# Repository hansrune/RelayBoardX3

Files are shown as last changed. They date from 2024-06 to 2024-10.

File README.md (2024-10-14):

# Relay board X3

Work in progress / still a prototype...

A DYI 3x relay board based on ESP32c3. This is a multi purpose board used for:

- `Garage doors` - controlling dual garage doors and control use of external switches
- `Ventilator / 1-phase small motor` 1-2-3 speed control. 

This board is tested with ESPhome and ESPEasy [firmware](#firmwares) (build instructions below), and is easily used with home automation systems that support MQTT auto discovery, the native Home Assistant API, and the many [controllers that ESPEasy supports](https://espeasy.readthedocs.io/en/latest/Controller/_Controller.html)

## Introduction

Some of the main features and benefits

- **3x galvanic isolated relays**
- **Car precense sensors**
    - Ultrasound sensor option
- **I2C support**
    - An I2C pin header with power supply is available to use with I2C sensors
    - ... or you can use the same GPIO pins for any other purpose of your choise
- **WiFi based**
    - This is almost a must have for most home automation systems
    - OTA support
    - Configuration backup, restore and bulk updates.
- **Firmware of your choise**
    - ESPEasy with Domoticz over http. Device creation uses virtual sensors
    - ESPEasy with Domotics and Home Assistant via MQTT. Device creation uses a MQTT configuration text file.
    - ESPHome to Home Assistant via MQTT and auto discovery
    - ESPHome to Domoticz via MQTT and auto discovery
    - ... and as the hardware supports using both Arduino and ESP-IF development kits, almost any other firmware can be created.
- **Seed Studio XIAO ESP32C3**
    - This device is shielded and comes with an external IPX antenna connector
    - FCC and CE regulations approved

<!--
## Setup and mounting - perhaps add later
-->

## Indicators

Each of the four valve outputs has a LED indicator at the back of the PCB

- LED D11 will indicate low level input from the flow meter
- LED D1
  - no change indicates out of power, device death/freeze or other
  - a duty cycle 1:1 will indicate a reset is ongoing
<!--
  - will blink with a duty cycle 1-4 or 4-1 to indicate valve closed or open
-->

## Implementation and design

The schematic diagram is [available here](KiCad//RelayBoardX3-schema-2.0.pdf). The [KiCad EDA](https://www.kicad.org/) project is in the [same folder](./KiCad)

### GPIO pin usage

| PIN | Capabilty | Function |
|---|---|---|
| GPIO2 | Acticve low output | LED D8 - not used |
| GPIO3 | Input with pull-up | J7 pin 2 |
| GPIO4 | Input with pull-up | J7 pin 1 |
| GPIO5 | Active high output | Relay 1 |
| GPIO6 | Active high output | Relay 2 |
| GPIO7 | I2C pulled up | SDL |
| GPIO8 | I2C pulled up | SDA |
| GPIO9 | Active low out | LED D8 - status |
| GPIO10 | Active high output | Relay 3 |
| GPIO20 | RX / 1-wire | Serial or 1-wire sensor or ultrasound |
| GPIO21 | TX / 1-wire | Serial or 1-wire sensor or ultrasound |

## Hardware - getting started

This project uses my [KiCad-lib-ESP32 repository](https://github.com/hansrune/KiCad-lib-ESP32.git) as a [git submodule](https://www.git-scm.com/book/en/v2/Git-Tools-Submodules). To check this out, use the following:

```bash
git clone --recurse-submodules https://github.com/hansrune/RelayBoardX4.git 
```

### Materials used

This project uses the [Seed Studio XIAO ESP32C3 RISC-V module](https://www.seeedstudio.com/Seeed-XIAO-ESP32C3-p-5431.html). This tiny device has proven to be more reliable than most ESP8266 modules used in earlier versions. This module also comes with an IPX connector for connecting an external antenna, and is delivered with a simple external antenna for good range. This device is also EMI shielded and certified.

Any available 12V DC power supply delivering 500mA or more should do for the control board. You will need to add the total power draw for the relays

There are many options and possible pinouts for DC-DC converters for the 12V to 5V conversion. A linear regulator (L7805) will need a heatsink, so a DC-DC converter is recommended.

<p align="center">
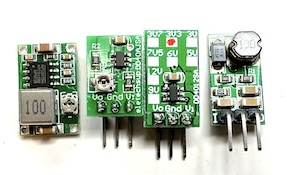
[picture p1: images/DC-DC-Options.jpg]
    
</p>

The MOSFETs need a low Vgs trigger voltage, i.e. well under 3V on full load. I have used Si2302/N025P for the N-channel, SOT-23 package.

Resistors are 0805 size. Screw terminals are 3.5mm, which is a tight fit when ferrules are being used.

For more information, use [this KiCad BOM](KiCad/RelayBoardX3-BOM.csv)

## Hardware assembly

Soldering a prototype by hand is possible if you have a steady hand and a small solder iron tip. A microscope is recommended to inspect the solder joints properly.

Recommend to do the SMD parts first, then other components. 

### Hardware tests

You should test at least the following **before adding the ESP32 module**:

- Attach a battery and check that the valve can be operated both NO and NC
- Add power and check that 5V conversion is OK
- Apply 5V to GPIO 5, 6, and 10 in turn to check that the output works with the relay LED indicators

## Firmwares

### ESPHome

ESPHome firmware can be set up from [this ESPHome configuration repository](https://github.com/hansrune/esphome-config) using the `test_relayx3_garage.yaml` or `test_relayx3_motor.yaml` file as a template

Follow the [README](https://github.com/hansrune/esphome-config) for instructions on what you will likely want to change.

By default, MQTT auto discovery is being used. This should work out of the box with Home Assistant, Domoticz and other that support [Home Assistant MQTT Auto Discovery](https://www.home-assistant.io/integrations/mqtt/#mqtt-discovery)

#### Garage doors control

In Home Assistant, the garage door controls can look like this:

<p align="center">
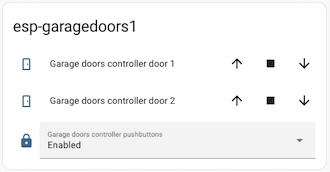
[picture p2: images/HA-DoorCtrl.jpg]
    
</p>

... and the closed state end stop sensors:

<p align="center">
    
</p>

#### Motor control

In Home Assistant, the device has this simple selector:

<p align="center">
    
</p>

### ESPEasy

ESPEasy can be used with a number of different controllers / home automation systms. A custom firmware build description is [available here](https://github.com/hansrune/ESPEasy-custom/blob/builds/custom/mega-20240822-1/README-custombuilds.md)

ESPEasy requires many settings. For configuration settings and rule files, you can upload the below sets of files. Please make sure to change name, unit number, controller IP addresses, NTP, syslog host and latitude/longitude. This configuration uses both a MQTT controller and a Domoticz controller. Change to what you need.

- For the garage control, use the files under [this page](./ESPEasy/garage)
- For the motor/ventilator control, use the files under [this page](./ESPEasy/motor/config.dat

## Wiring

### Dual garage door wiring

This dual garage door setup uses a pulse driven elevator, and has end stop switches for the closed position. There is no end stops for the open position, meaning that the open state simply reflects not closed.

A `RX-Multi` receiver is used in parallel with the relay board. This is operated by remote control units from a car.

We have outdoor push buttons to operate the garage doors. These are disabled via relay #1 when our home alarm state is away or night. The power on state is that these buttons are enabled.

<p align="center">
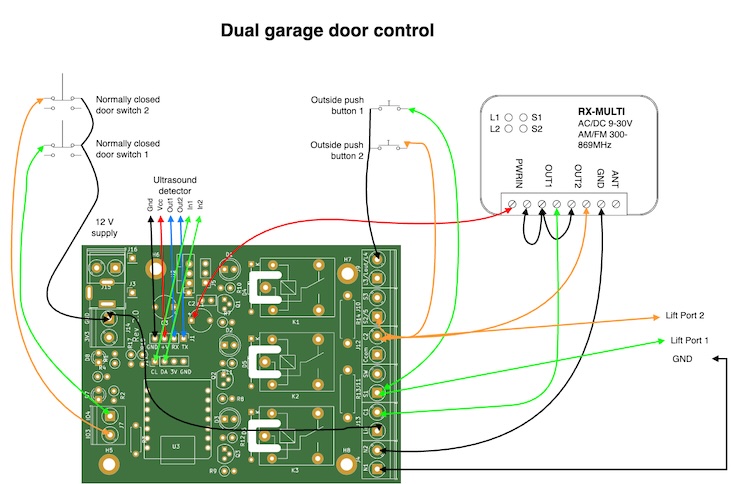
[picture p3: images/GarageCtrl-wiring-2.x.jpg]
    
</p>

### Motor control wiring

This setup is a simple 1-2-3 speed motor control for a ventilator. Can work in parallel with a 1-2-3 switch, where you will get the highest speed selected via contoller or switch.

<p align="center">
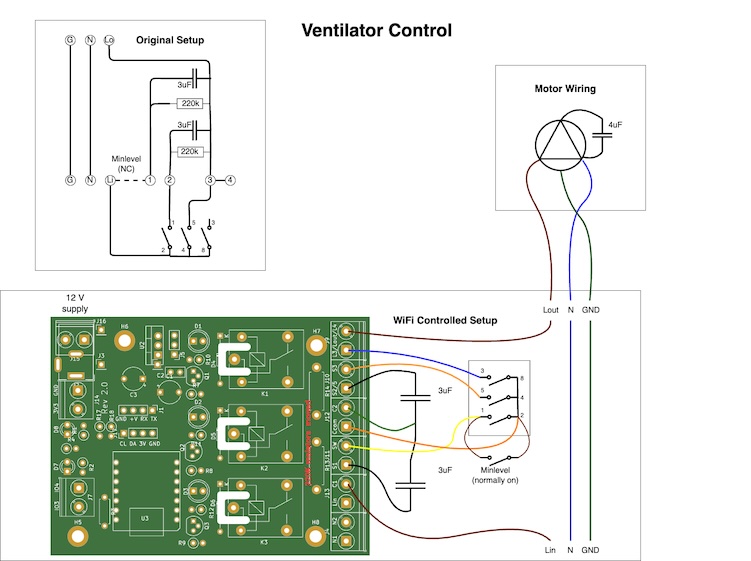
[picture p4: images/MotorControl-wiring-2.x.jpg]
    
</p>

## Licensing

This project is licensed under the [GNU General Public License v3.0](GNU-LICENSE-V3.txt) for the software, [CERN-OHL-W](OHL-LICENSE.txt) for the hardware, and [CC BY-SA](CC-BY-SA-LICENCE.txt) for the documentation and ideas.

<p align="center" width="100%">
    
</p>

<!-- 
| **Open Source Licenses** | |
| ---|---|
| Hardware | [CERN-OHL-W](OHL-LICENSE.txt) |
| Software | [GNU General Public License v3.0](GNU-LICENSE-V3.txt) |
| Documentation / idea | [CC BY-SA](CC-BY-SA-LICENCE.txt) |
-->

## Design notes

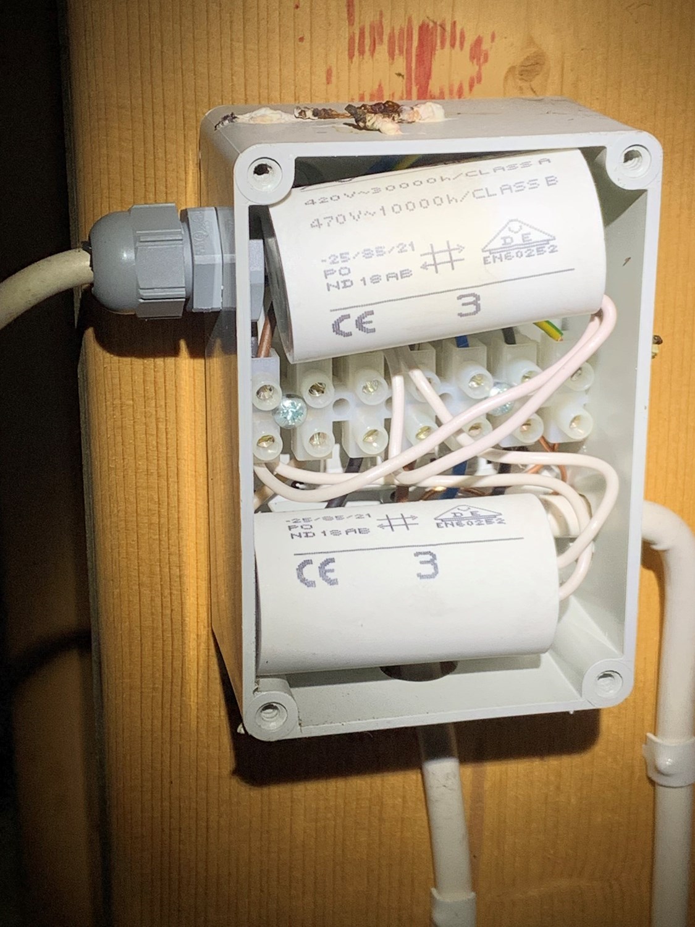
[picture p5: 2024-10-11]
KiCad/vendorinfo/ULVbox.jpg

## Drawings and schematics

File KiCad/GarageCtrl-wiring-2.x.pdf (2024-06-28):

# Dual garage door control

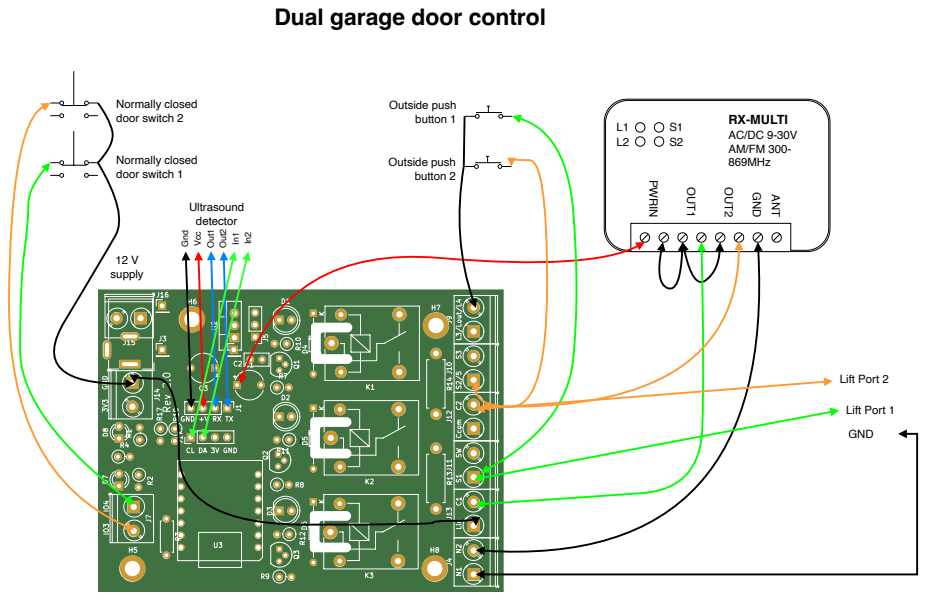
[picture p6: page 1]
RX-MULTI; AC/DC 9-30V AM/FM 300- 869MHz; PWRIN; OUT1; OUT2; GND; ANT; Lift Port 2; Lift Port 1; Outside push button 1; Outside push button 2; Normally closed door switch 2; Normally closed door switch 1; 12 V supply; Ultrasound detector; Gnd; Vcc; Out1; Out2

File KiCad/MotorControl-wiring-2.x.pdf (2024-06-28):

# Ventilator Control

### Original Setup

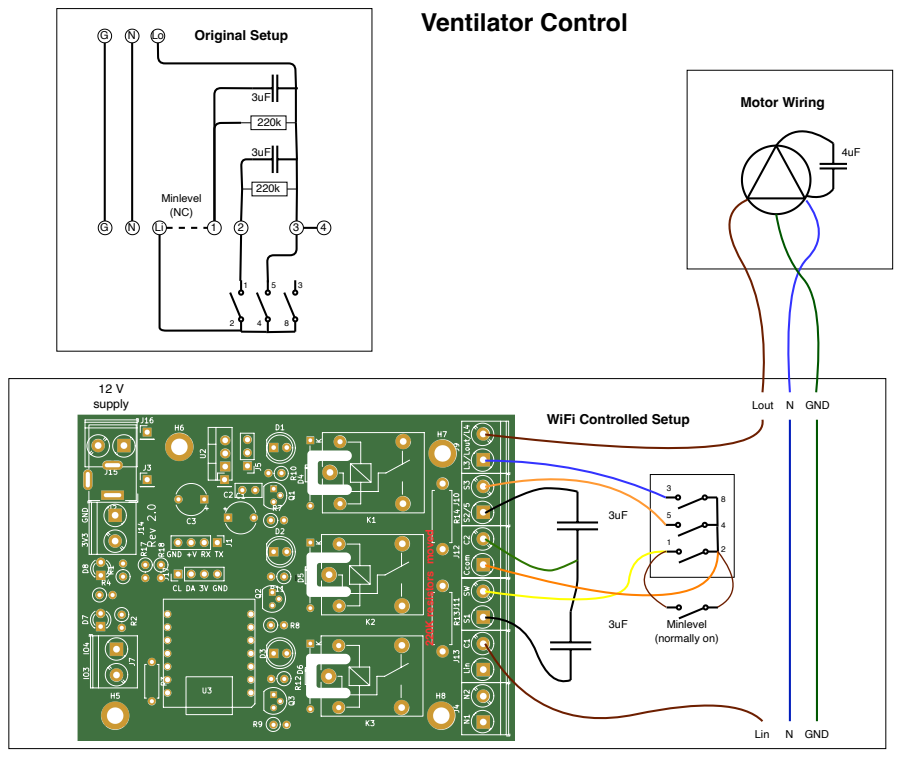
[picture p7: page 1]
12 V supply; Lin; N GND; Lout N GND; Minlevel (normally on); 220K resistors moved; Minlevel (NC); Motor Wiring

WiFi Controlled Setup

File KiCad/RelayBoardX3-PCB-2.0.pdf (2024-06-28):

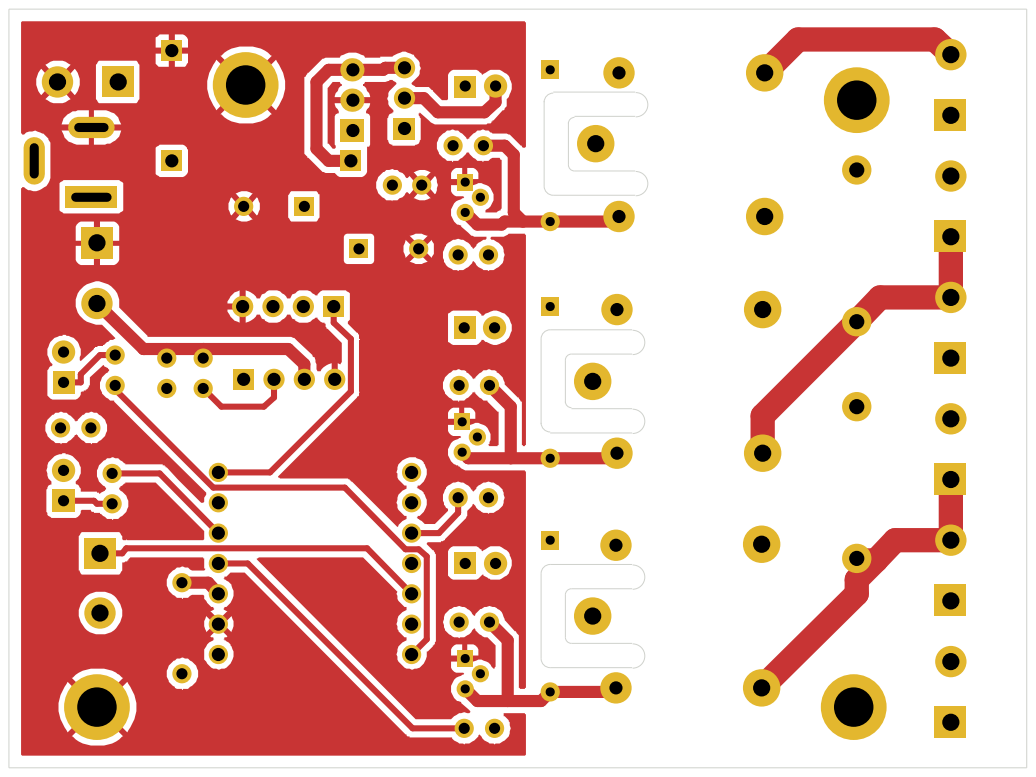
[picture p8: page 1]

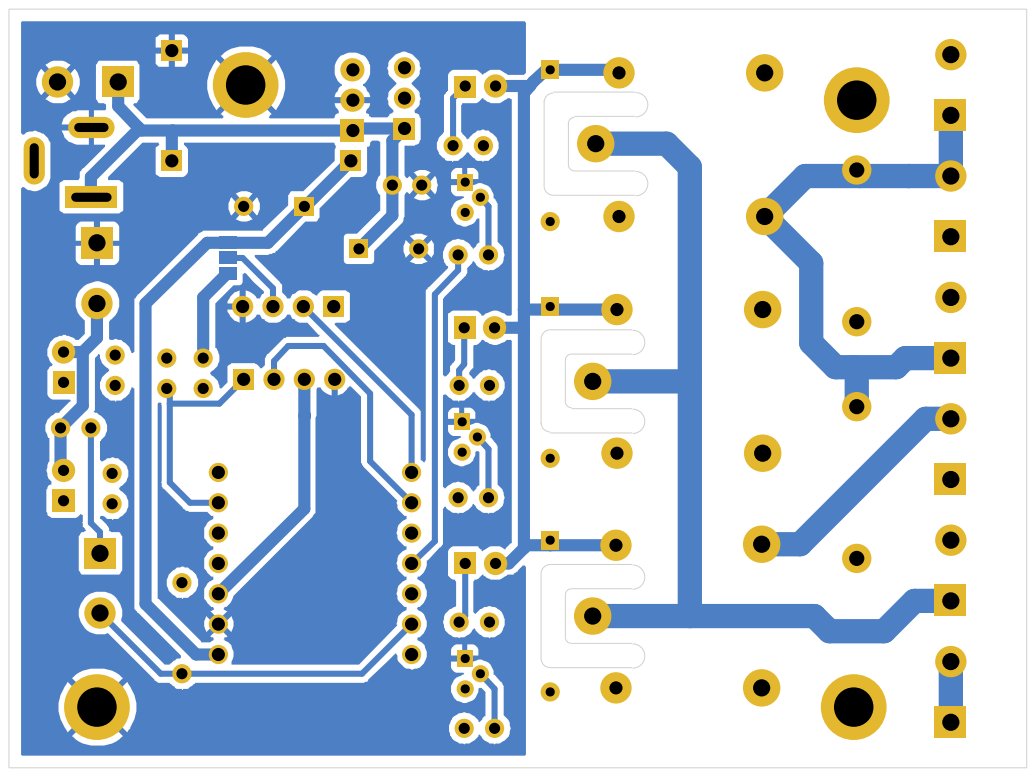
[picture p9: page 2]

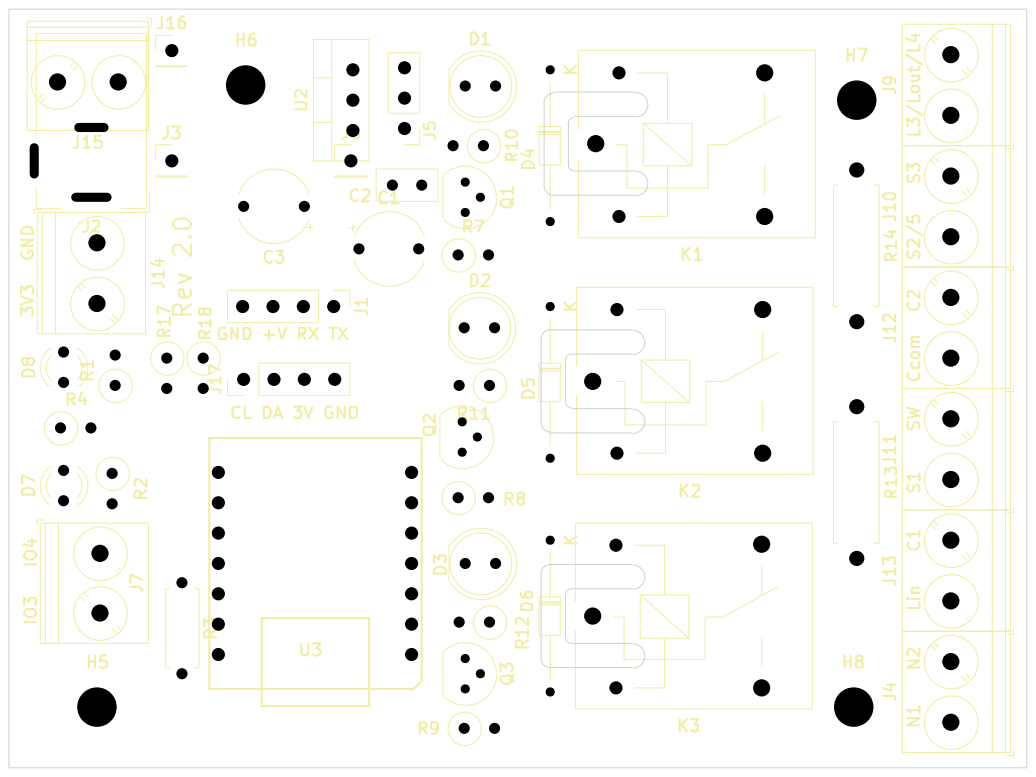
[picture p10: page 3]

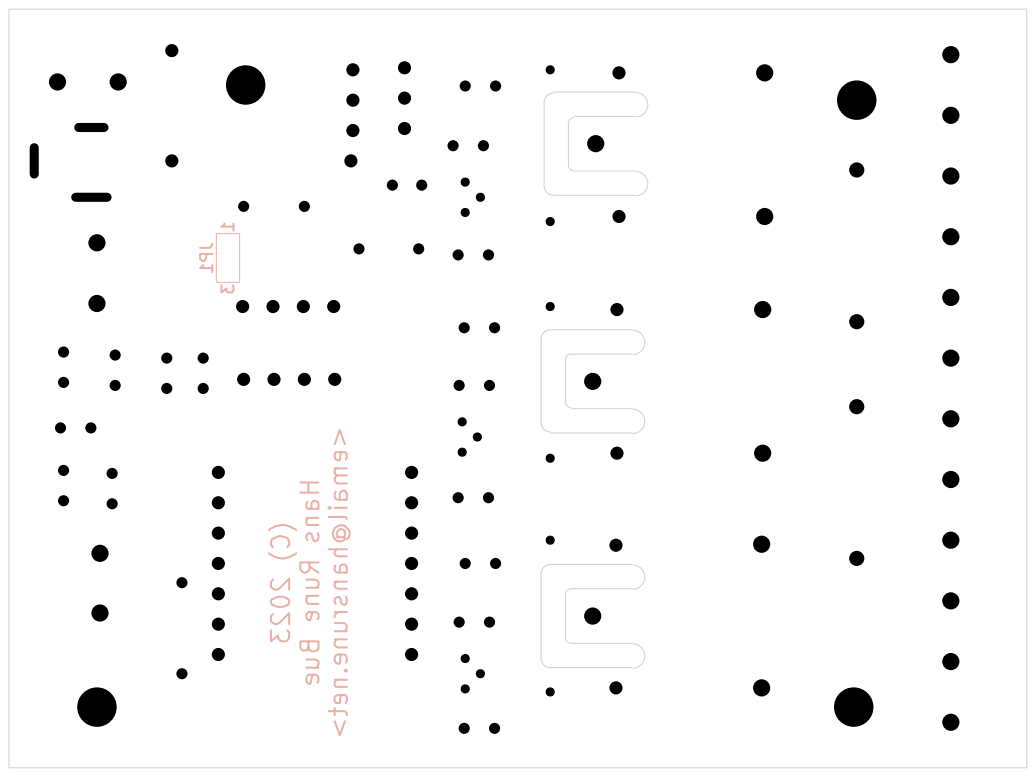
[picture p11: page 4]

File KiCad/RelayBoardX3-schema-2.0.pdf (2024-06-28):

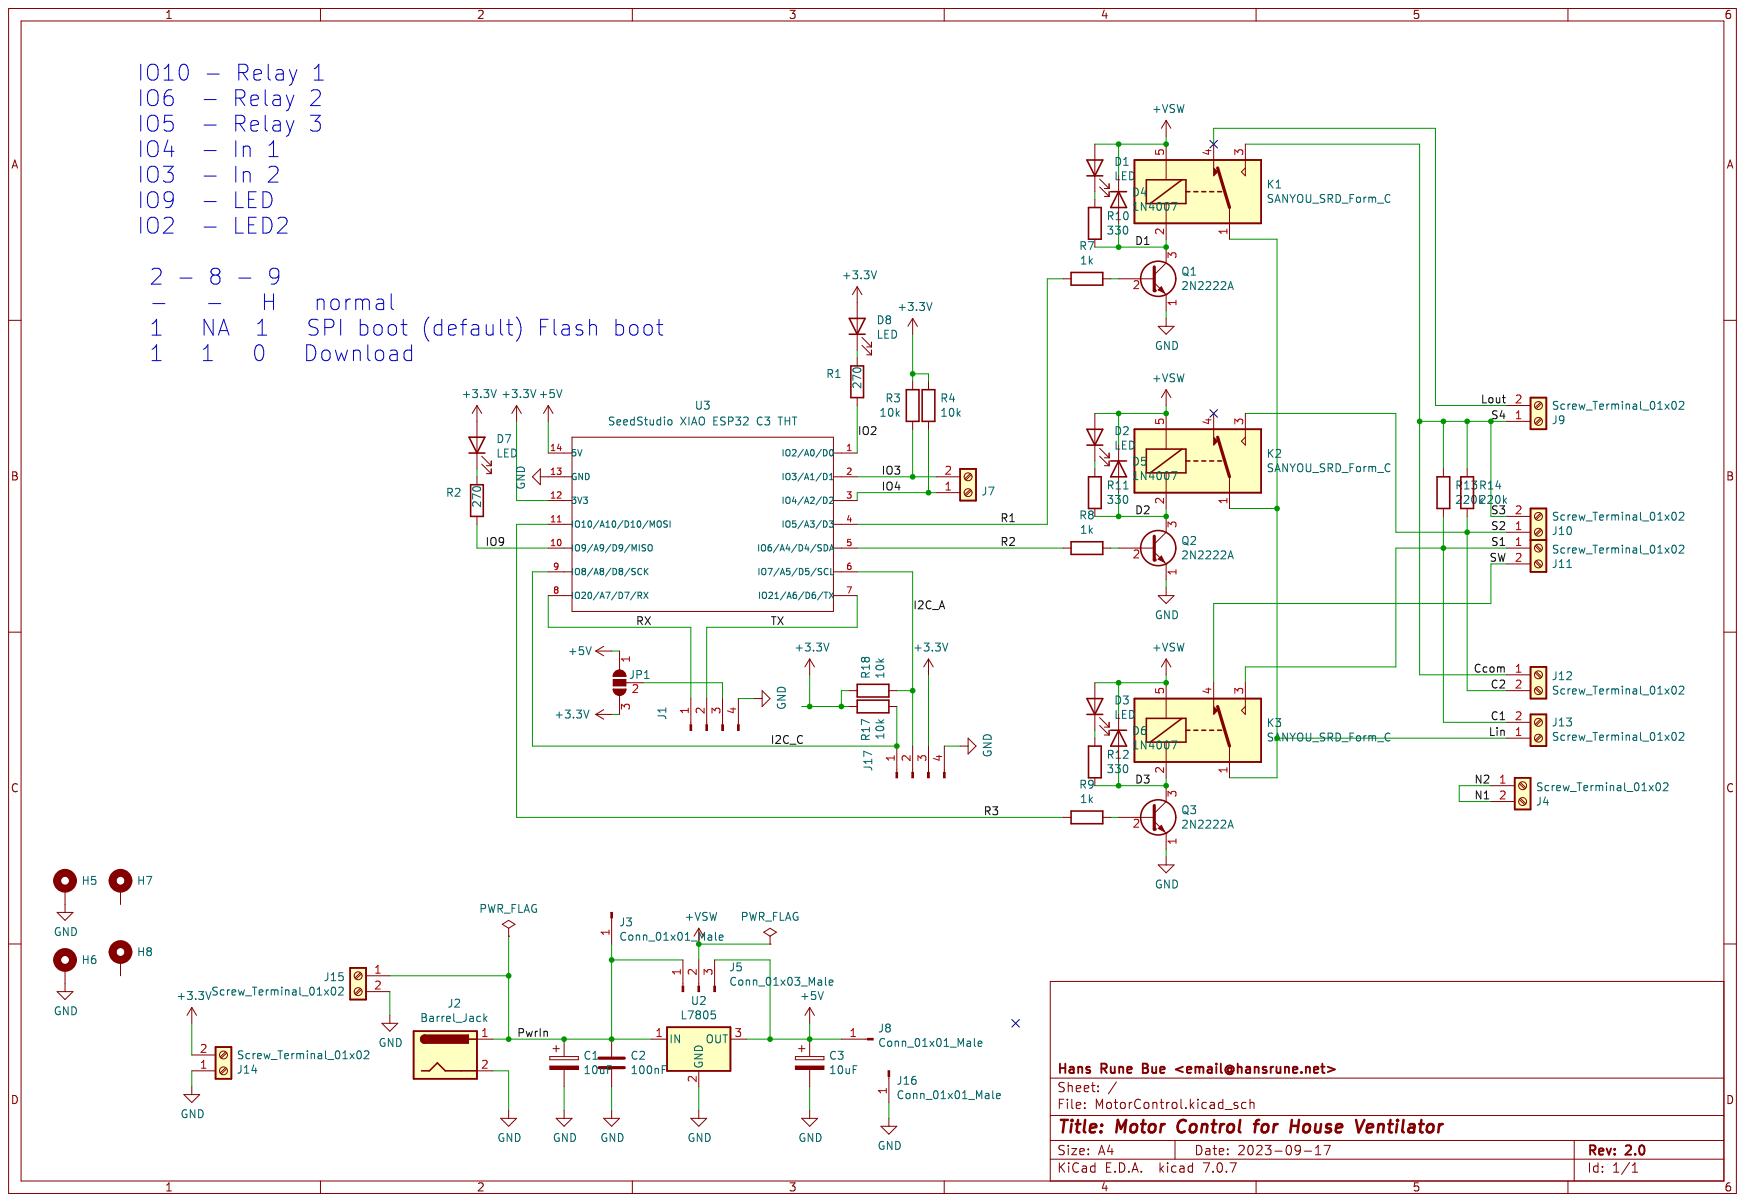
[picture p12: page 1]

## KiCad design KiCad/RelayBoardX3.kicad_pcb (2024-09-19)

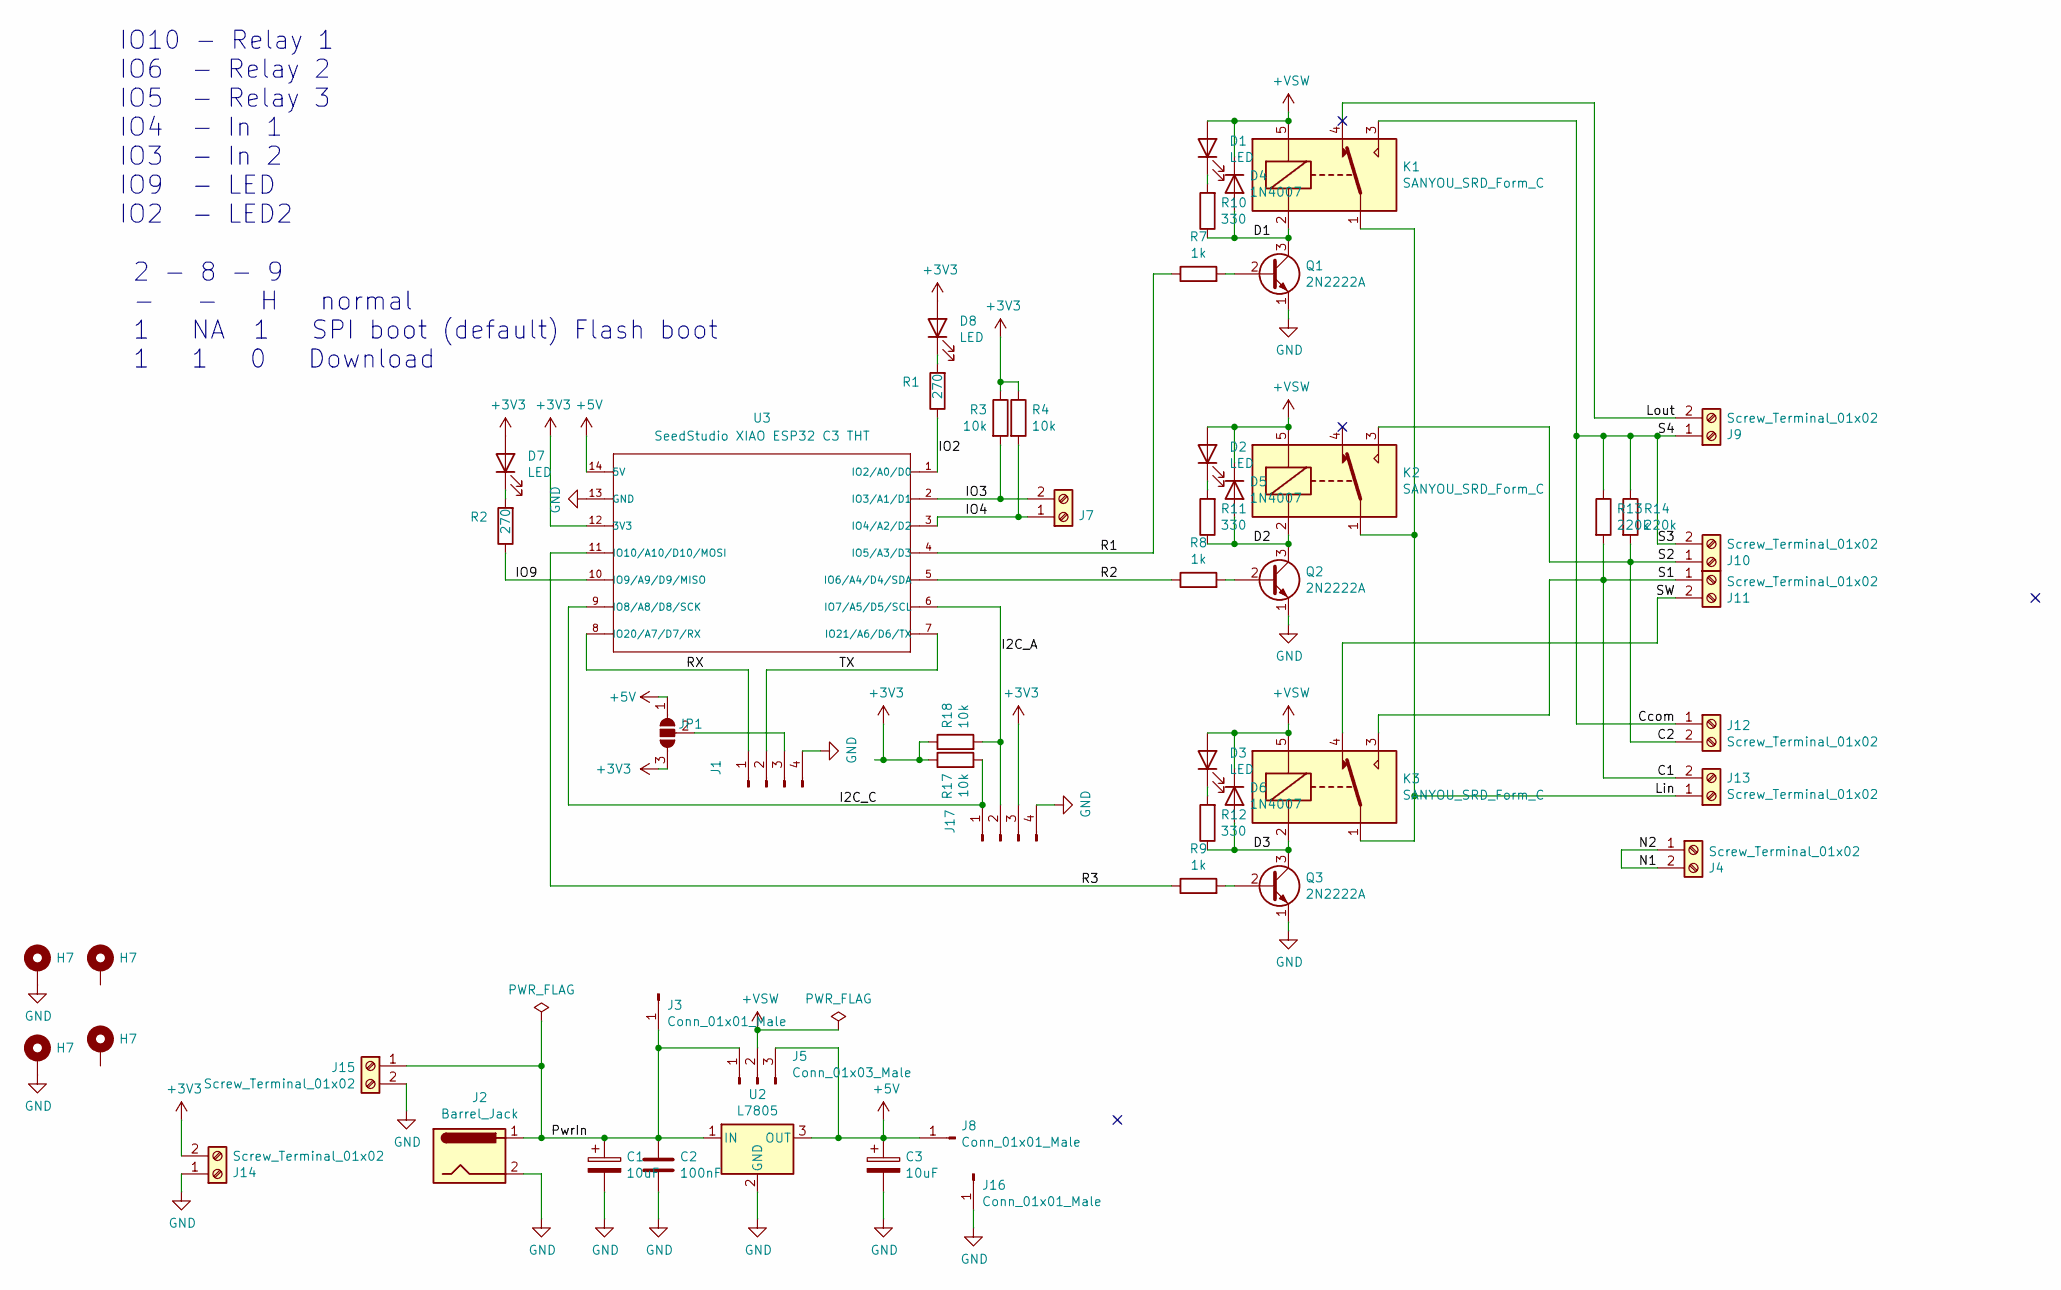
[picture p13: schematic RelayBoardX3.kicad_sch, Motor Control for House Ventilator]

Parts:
C1, C3: 10uF; CP_Radial_Tantal_D6.0mm_P5.00mm
C2: 100nF; C_Disc_D5.0mm_W2.5mm_P2.50mm
D1, D2, D3: LED; LED_D5.0mm_Clear
D4, D5, D6: 1N4007; D_DO-34_SOD68_P12.70mm_Horizontal
D7, D8: LED; LED_D3.0mm_Clear
H7: MountingHole_Pad; MountingHole_3.2mm_M3_ISO14580_Pad
J1, J17: Conn_01x04_Male; PinHeader_1x04_P2.54mm_Vertical
J2: Barrel_Jack; BarrelJack1
J3, J8, J16: Conn_01x01_Male; PinHeader_1x01_P2.54mm_Vertical
J4, J7, J9, J10, J11, J12, J13, J14, J15: Screw_Terminal_01x02; TerminalBlock_Phoenix_PT-1,5-2-5.0-H_1x02_P5.00mm_Horizontal
J5: Conn_01x03_Male; PinHeader_1x03_P2.54mm_Vertical
JP1: SolderJumper_3_Open; SolderJumper-3_P1.3mm_Open_Pad1.0x1.5mm_NumberLabels
K1, K2, K3: SANYOU_SRD_Form_C; Relay_SPDT_SANYOU_SRD_CutOut
Q1, Q2, Q3: 2N2222A; TO-92
R1, R2: 270; R_Axial_DIN0207_L6.3mm_D2.5mm_P2.54mm_Vertical
R3: 10k; R_Axial_DIN0207_L6.3mm_D2.5mm_P7.62mm_Horizontal
R4, R17, R18: 10k; R_Axial_DIN0207_L6.3mm_D2.5mm_P2.54mm_Vertical
R7, R8, R9: 1k; R_Axial_DIN0207_L6.3mm_D2.5mm_P2.54mm_Vertical
R10, R11, R12: 330; R_Axial_DIN0207_L6.3mm_D2.5mm_P2.54mm_Vertical
R13, R14: 220k; R_Axial_DIN0411_L9.9mm_D3.6mm_P12.70mm_Horizontal
U2: L7805; TO-220-3_Vertical
U3: SeedStudio XIAO ESP32 C3 THT; XIAO_ESP32C3_THT

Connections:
+3V3: D7.2 (A), D8.2 (A), J14.2, J17.3, JP1.3 (B), R3.1, R4.1, R17.1, R18.1, U3.12 (3V3)
+5V: C3.1, J5.3, J8.1, JP1.1 (A), U2.3 (OUT), U3.14 (5V)
+VSW: D1.2 (A), D2.2 (A), D3.2 (A), D4.1 (K), D5.1 (K), D6.1 (K), J5.2, K1.5, K2.5, K3.5
/C1: J11.1, J13.2, K3.3, R13.2
/C2: J10.1, J12.2, K2.3, R14.2
/Ccom: J9.1, J10.2, J12.1, K1.3, R13.1, R14.1
/D1: D4.2 (A), K1.2, Q1.3 (C), R10.1
/D2: D5.2 (A), K2.2, Q2.3 (C), R11.1
/D3: D6.2 (A), K3.2, Q3.3 (C), R12.1
/I2C_A: J17.2, R18.2, U3.6 (IO7/A5/D5/SCL)
/I2C_C: J17.1, R17.2, U3.9 (IO8/A8/D8/SCK)
/IO2: R1.1, U3.1 (IO2/A0/D0)
/IO3: J7.2, R3.2, U3.2 (IO3/A1/D1)
/IO4: J7.1, R4.2, U3.3 (IO4/A2/D2)
/IO9: R2.1, U3.10 (IO9/A9/D9/MISO)
/Lin: J13.1, K1.1, K2.1, K3.1
/Lout: J9.2, K1.4
/N1: J4.1, J4.2
/PwrIn: C1.1, C2.1, J2.1, J3.1, J5.1, J15.1, U2.1 (IN)
/R1: R7.1, U3.4 (IO5/A3/D3)
/R2: R8.1, U3.5 (IO6/A4/D4/SDA)
/R3: R9.1, U3.11 (IO10/A10/D10/MOSI)
/RX: J1.1, U3.8 (IO20/A7/D7/RX)
/SW: J11.2, K3.4
/TX: J1.2, U3.7 (IO21/A6/D6/TX)
GND: C1.2, C2.2, C3.2, H7.1, J1.4, J2.2, J14.1, J15.2, J16.1, J17.4, Q1.1 (E), Q2.1 (E), Q3.1 (E), U2.2 (GND), U3.13 (GND); also elsewhere on the board
unnamed: D1.1 (K), R10.2
unnamed: D2.1 (K), R11.2
unnamed: D3.1 (K), R12.2
unnamed: D7.1 (K), R2.2
unnamed: D8.1 (K), R1.2
unnamed: J1.3, JP1.2 (C)
unnamed: Q1.2 (B), R7.2
unnamed: Q2.2 (B), R8.2
unnamed: Q3.2 (B), R9.2

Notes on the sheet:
IO10 - Relay 1 IO6 - Relay 2 IO5 - Relay 3 IO4 - In 1 IO3 - In 2 IO9 - LED IO2 - LED2 2 - 8 - 9 - - H normal 1 NA 1 SPI boot (default) Flash boot 1 1 0 Download

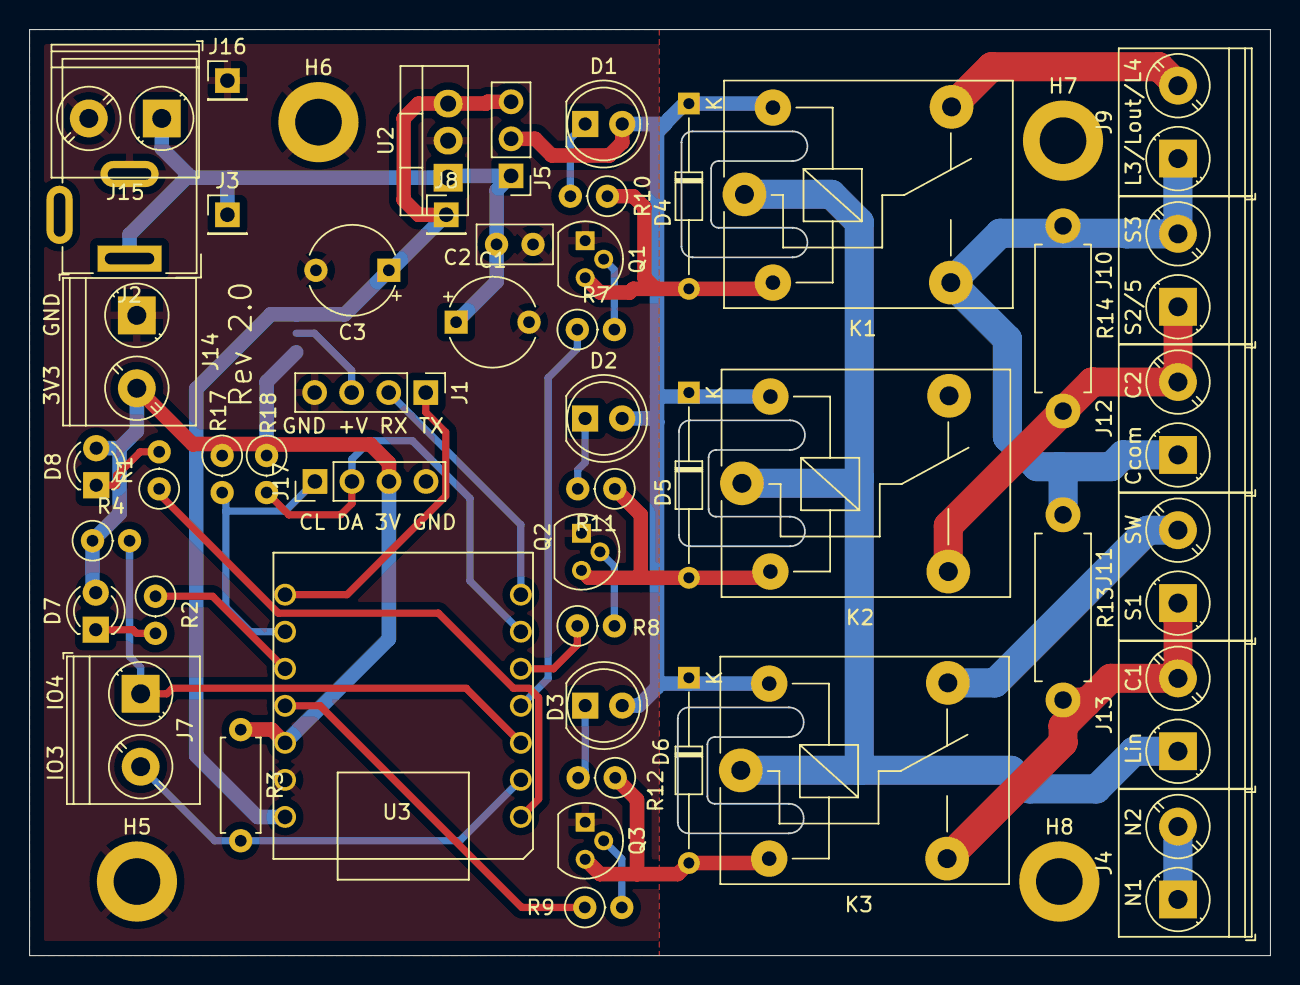
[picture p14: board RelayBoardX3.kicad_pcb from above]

Board: 2 copper layers, 85.1 x 63.5 mm, 54 parts (1 on the bottom side), 35 nets.

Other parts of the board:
H5, H6, H8: MountingHole_Pad; MountingHole_3.2mm_M3_ISO14580_Pad

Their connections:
GND: H5.1, H6.1; also elsewhere on the board

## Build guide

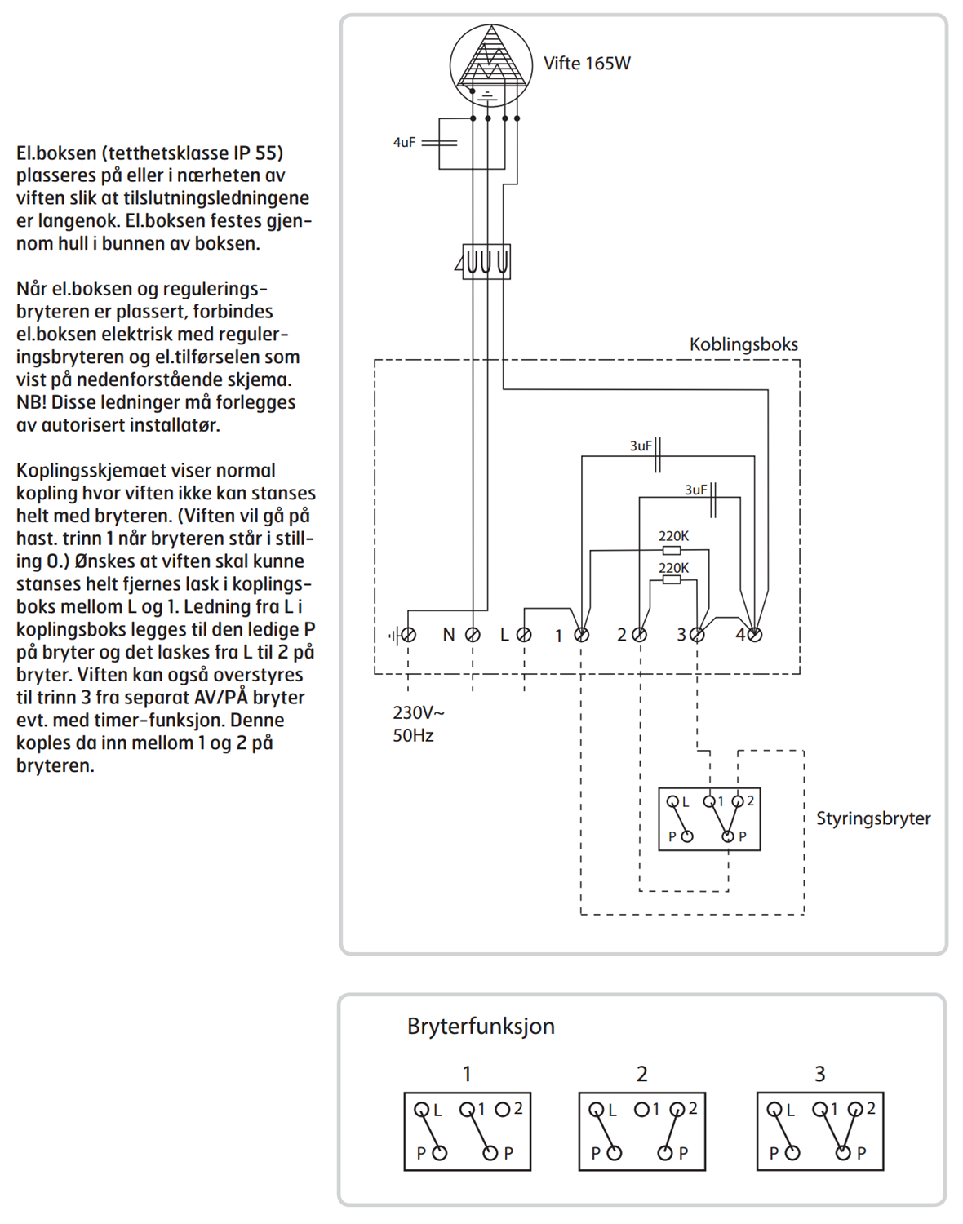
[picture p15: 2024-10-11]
KiCad/vendorinfo/Wiring-ULV120.png

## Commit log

2024-06-28 Version 2.0 KiCad project added
    [RelayBoardX3.kicad_pcb, RelayBoardX3.kicad_sch]
2024-09-19 New 3D model
    [RelayBoardX3.kicad_pcb]
2024-10-11 Added color specs to KiCAD schema
    [RelayBoardX3.kicad_sch]
2024-10-11 Add wiring diagrams
2024-10-11 Add wiring diagrams to README
2024-10-12 Home Assistant firmware for motor 1-2-3 control added

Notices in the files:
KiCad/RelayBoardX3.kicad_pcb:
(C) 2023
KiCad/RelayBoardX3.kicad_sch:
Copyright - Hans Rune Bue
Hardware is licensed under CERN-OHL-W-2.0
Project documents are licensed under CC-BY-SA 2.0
